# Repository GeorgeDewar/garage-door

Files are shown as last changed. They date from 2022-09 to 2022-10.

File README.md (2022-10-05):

# garage-door

ESP8266-based garage door controller (status and control via MQTT)

This is a personal project to control my garage door opener remotely using my phone. It's designed specifically around my garage door opener, which is pretty old and I'm not even sure what make and model it is. It comprises a circuit containing a NodeMCU ESP8266 dev board, some components, and a small modification to the door opener to expose additional signals.

My opener has a series of screw terminals, notably:

- GND - common ground for all other terminals
- P/B (push button) - a 5V signal that when pulled low, causes the door to open or close. I believe it is equivalent to the button on the side of the unit
- 15V - a supply of power, which is poorly regulated so is often more like 18-20V

I had two goals. Firstly, to install a button inside the house with an LED that shows the status of the door.  For that I used the [PDL 680TMNPB-WH](https://www.scottelectrical.co.nz/shop/switch-gear-wiring-devices/modulesmechs/specialty/pdl-switch-elv-tactile-red-neon/) which combines a momentary switch (button) with an LED. But the LED has a built-in resistor such that it is designed to take a 24V input, which means I can't drive it easily from a microcontroller. So, I elected to use the 15V supply to power the LED. In fact, even with 5V the LED is visible, but dim. 15-20V is good and bright.

The LED is on when the door is open, flashing when it is partially open (e.g. opening or closing), and off when it is closed. The button is connected directly (electrically speaking) to the P/B terminal on the garage door so that it will work even if my device is unpowered.

The second goal is to control it from my phone. That means being able to see the status, and actuate the door. To achieve this, I made the microcontroller send to Home Assistant via MQTT status updates, and accept commands, which cause it to pull the P/B signal low to simulate a button press.

The list of terminals I gave above did not include any terminal which can be used to detect the state of the door. But the opener does have two microswitches that are actuated by cams to tell it when it has fully closed or fully opened. These are also 5V signals that are pulled low by the microswitches. I tapped into these and exposed them, along with the other three termials, on a convenient DB9 socket which I mounted on the opener. Using these two signals, my microcontroller can tell if the door is open, closed, or partially open. The fourth state, where both signals are low, should never occur.

This repository contains the firmware for the ESP8266, and the circuit diagram and veroboard layout I used. I designed in support for end-user WiFi setup, but unfortunately the MQTT settings are hard-coded. I don't know if I will ever bother to change that since I am not highly likely to have additional users to support, and if I do get some, they can just change the code.

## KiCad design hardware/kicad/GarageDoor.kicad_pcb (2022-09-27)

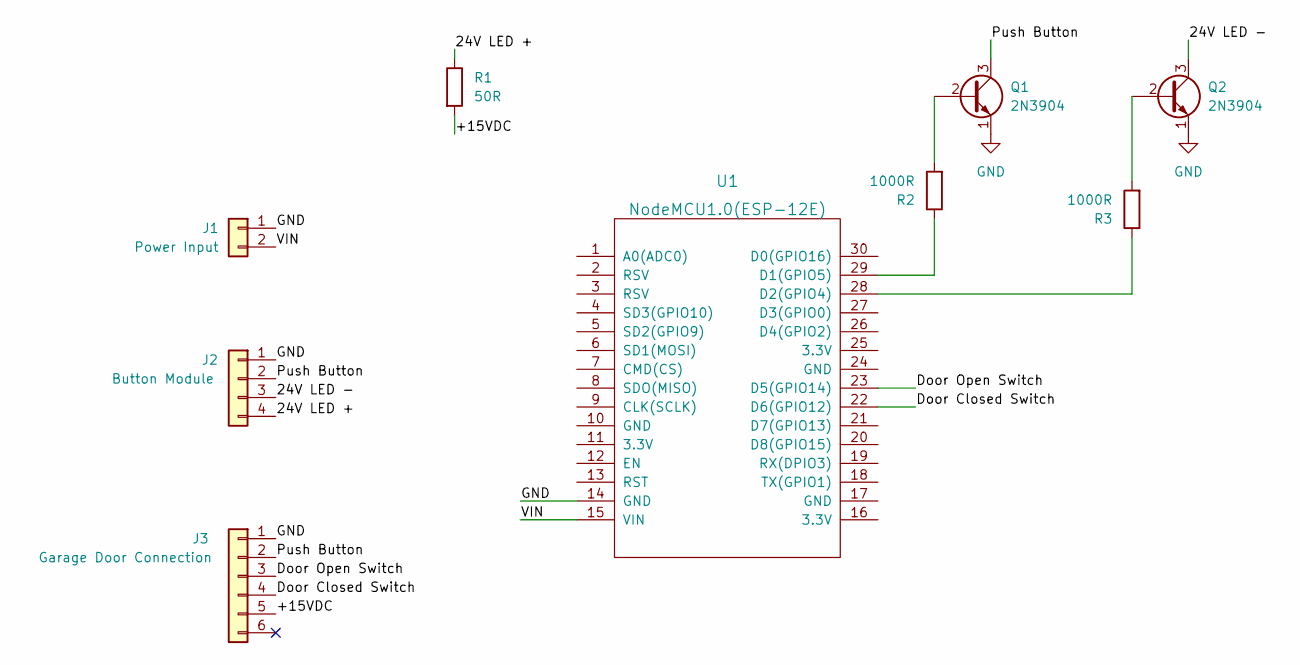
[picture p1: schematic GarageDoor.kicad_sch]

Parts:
J1: Power Input; PinHeader_1x02_P2.54mm_Vertical
J2: Button Module; PinHeader_1x04_P2.54mm_Vertical
J3: Garage Door Connection; PinHeader_1x06_P2.54mm_Vertical
Q1, Q2: 2N3904; TO-92_Inline
R1: 50R; R_Bare_Metal_Element_L16.3mm_W4.8mm_P15.30mm
R2, R3: 1000R; R_Bare_Metal_Element_L16.3mm_W4.8mm_P15.30mm
U1: NodeMCU1.0(ESP-12E); NodeMCU1.0(12-E)

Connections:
/24V LED +: J2.4, R1.1
/24V LED -: J2.3, Q2.3 (C)
/+15VDC: J3.5, R1.2
/Door Closed Switch: J3.4, U1.22 (D6(GPIO12))
/Door Open Switch: J3.3, U1.23 (D5(GPIO14))
/Push Button: J2.2, J3.2, Q1.3 (C)
/VIN: J1.2, U1.15 (VIN)
GND: J1.1, J2.1, J3.1, Q1.1 (E), Q2.1 (E), U1.14 (GND)
unnamed: Q1.2 (B), R2.2
unnamed: Q2.2 (B), R3.2
unnamed: R3.1, U1.28 (D2(GPIO4))
unnamed: R2.1, U1.29 (D1(GPIO5))

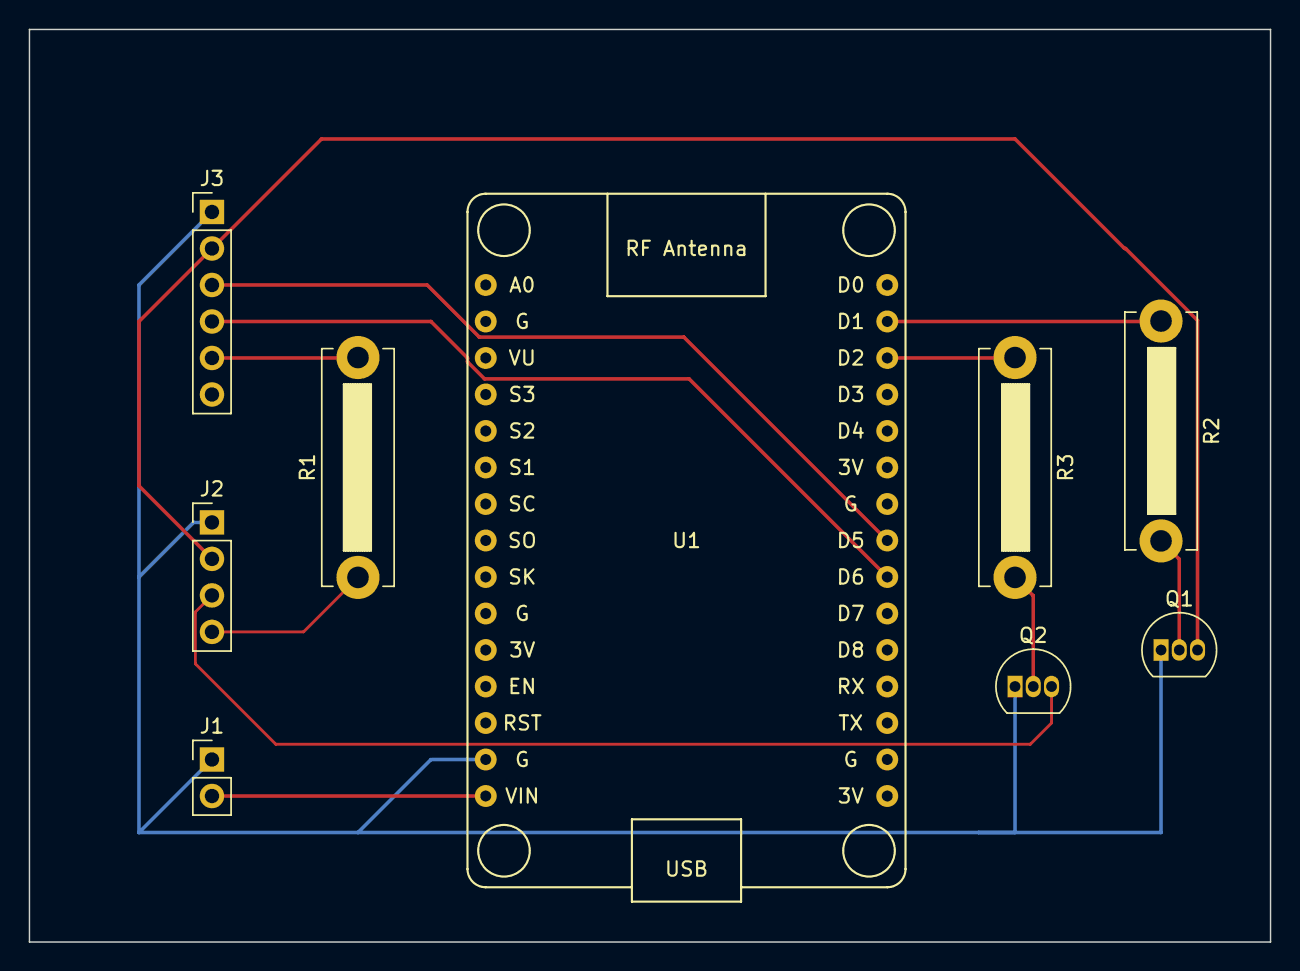
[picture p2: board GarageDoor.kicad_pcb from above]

Board: 2 copper layers, 86.4 x 63.5 mm, 9 parts (0 on the bottom side), 12 nets.

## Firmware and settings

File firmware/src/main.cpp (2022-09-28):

#include <ESP8266WiFi.h>
#include <WiFiManager.h>
#include <EasyButton.h>
#include <EspMQTTClient.h>

// NodeMCU board pins
#define BUTTON_FLASH        D3
#define OUTPUT_PUSH_BUTTON  D1
#define OUTPUT_24V_LED      D2
#define INPUT_DOOR_OPEN     D5
#define INPUT_DOOR_CLOSED   D6

// Flashing speeds
#define FLASHING_SLOW_MS    500
#define FLASHING_FAST_MS    250

// Possible states for the door to be in, based on the microswitch positions
enum DoorState {
  OPEN,
  DOOR_CLOSED,
  PARTIAL,      // neither open nor closed, which means opening, closing, or just stopped part way
  INVALID,      // i.e. both open and closed, shouldn't be possible
  UNKNOWN       // the default state prior to reading it for the first time, or to force an update
};

// Objects
WiFiManager wifiManager;
EasyButton flashButton(BUTTON_FLASH);
EspMQTTClient mqttClient(
  "192.168.20.68",
  1883,            // It is mandatory here to allow these constructors to be distinct from those with the Wifi handling parameters
  "DVES_USER",     // Omit this parameter to disable MQTT authentification
  "DVES_PASS",     // Omit this parameter to disable MQTT authentification
  "GarageDoor");

// Variables
DoorState door_state = UNKNOWN;
unsigned long lastBlinkMillis = 0; // when the loop function last ran
int lastFlashingState = LOW;

// Interrupt service routine for the interrupt triggered by the Flash button
void flashButtonISR()
{
  flashButton.read();
}

// Callback function to be called when the Flash button is pressed. Erase all configuration.
void onFlashButtonPressed() {
  Serial.println("Flash button has been pressed! Resetting...");
  ESP.eraseConfig();
  delay(500);
  ESP.restart();
}

// Simulate a press of the open/close button
void pressDoorButton() {
  digitalWrite(OUTPUT_PUSH_BUTTON, HIGH); // depress the button
  delay(250);
  digitalWrite(OUTPUT_PUSH_BUTTON, LOW); // back to high impedance
}

// Called when MQTT connection established
void onConnectionEstablished()
{
  // Subscribe to commands. For any command, we press the button. That's all we can do.
  mqttClient.subscribe("garage-door/command", [](const String & payload) {
    Serial.println(payload);
    pressDoorButton();
  });

  // Announce that we are online
  mqttClient.publish("garage-door/availability", "online");

  // Force a status update, in case we've been offline for a while
  door_state = DoorState::UNKNOWN;
}

// Flash the internal LED the specified number of times
void flashBuiltInLed(int times) {
  for(int i=0; i<times; i++) {
    digitalWrite(LED_BUILTIN, LOW);
    delay(200);
    digitalWrite(LED_BUILTIN, HIGH);
    if (i < times) delay(200);
  }
}

// Called once on startup
void setup() {
  // Initialise our inputs and outputs
  pinMode(BUTTON_FLASH, INPUT_PULLUP);
  pinMode(LED_BUILTIN, OUTPUT);
  pinMode(OUTPUT_PUSH_BUTTON, OUTPUT);    // note: when low, the external transistor is high impedance (floating)
  pinMode(OUTPUT_24V_LED, OUTPUT);        // note: when low, the external transistor is high impedance (floating)
  pinMode(INPUT_DOOR_OPEN, INPUT);
  pinMode(INPUT_DOOR_CLOSED, INPUT);

  // Write the initial states of our outputs
  digitalWrite(LED_BUILTIN, LOW);         // Turn the LED on
  digitalWrite(OUTPUT_PUSH_BUTTON, LOW);  // Don't be pressing the button
  digitalWrite(OUTPUT_24V_LED, LOW);      // Main LED off to start with

  // Begin serial communication for debugging
  Serial.begin(115200);

  // Work out and announce our device name
  String deviceName = "GarageDoor-" + String(ESP.getChipId(), HEX);
  Serial.print("\nHello! Device name = ");
  Serial.println(deviceName);

  // Captive portal for first-time WiFi setup
  wifiManager.setConfigPortalTimeout(120); // after two minutes, give up on connecting
  if (wifiManager.autoConnect(deviceName.c_str(), NULL)) {
    // We're connected, so we set the host name and announce our IP address
    WiFi.hostname(deviceName);
    Serial.println("WiFi connected: IP = " + WiFi.localIP().toString());

    // Always run the web portal so the device can be reconfigured
    wifiManager.startWebPortal();
  } else {
    Serial.println("Failed to connect to WiFi; in offline mode");
  }

  // Configure the MQTT client
  mqttClient.enableDebuggingMessages();
  mqttClient.enableLastWillMessage("garage-door/availability", "offline");

  // Configure the Flash button
  flashButton.begin();
  flashButton.onPressed(onFlashButtonPressed);
  flashButton.enableInterrupt(flashButtonISR);

  // Flash built-in LED to indicate startup complete
  flashBuiltInLed(3); // really 2 flashes as LED already on
}

// the loop function runs over and over again forever
void loop() {
  // Let the libraries do their processing
  flashButton.read();
  wifiManager.process();
  mqttClient.loop();

  // Determine the state of the door based on the microswitches
  int doorClosed = digitalRead(INPUT_DOOR_CLOSED);
  int doorOpen = digitalRead(INPUT_DOOR_OPEN);
  DoorState new_state;
  if (doorClosed == LOW && doorOpen == HIGH) {
    new_state = DoorState::DOOR_CLOSED;
  } else if (doorClosed == HIGH && doorOpen == LOW) {
    new_state = DoorState::OPEN;
  } else if (doorClosed == HIGH && doorOpen == HIGH) {
    new_state = DoorState::PARTIAL;
  } else {
    new_state = DoorState::INVALID;
  }

  // Handle the LED output
  if (new_state == DoorState::DOOR_CLOSED) {
    digitalWrite(OUTPUT_24V_LED, LOW);
  } else if (new_state == DoorState::OPEN) {
    digitalWrite(OUTPUT_24V_LED, HIGH);
  } else {
    // we are flashing
    unsigned long currentTime = millis();
    if (currentTime > lastBlinkMillis + FLASHING_SLOW_MS) {
      lastBlinkMillis = currentTime;
      lastFlashingState = 1 - lastFlashingState;
      digitalWrite(OUTPUT_24V_LED, lastFlashingState);
    }
  }

  // If nothing has changed, then there's nothing else we need to do
  if (door_state == new_state) return;

  // Figure out what message to publish based on the old and new state
  // Publishing will do nothing if the client is not connected
  if (new_state == DoorState::DOOR_CLOSED) {
    Serial.println("Door has closed");
    mqttClient.publish("garage-door/state", "closed");
  } else if (new_state == DoorState::OPEN) {
    Serial.println("Door has opened");
    mqttClient.publish("garage-door/state", "open");
  } else if (new_state == DoorState::PARTIAL && door_state == DoorState::OPEN) {
    // transition from OPEN to PARTIAL means we are closing
    Serial.println("Door is closing");
    mqttClient.publish("garage-door/state", "closing");
  } else if (new_state == DoorState::PARTIAL && door_state == DoorState::DOOR_CLOSED) {
    // transition from CLOSED to PARTIAL means we are opening
    Serial.println("Door is opening");
    mqttClient.publish("garage-door/state", "opening");
  } else if (new_state == DoorState::PARTIAL && door_state == DoorState::UNKNOWN) {
    // it must have been partially open on start-up
    Serial.println("Door is partially open, assuming closing");
    mqttClient.publish("garage-door/state", "closing");
  } else if (new_state == DoorState::INVALID) {
    // we have a problem
    Serial.println("Door state is invalid (both microswitches LOW)");
    mqttClient.publish("garage-door/state", "closing");
  }

  // Now update door_state since we don't need the old value any more
  door_state = new_state;
}

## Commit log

2022-09-26 Get LED output working right
2022-09-26 Remove old Arduino IDE based version
2022-09-27 Add Kicad files
    [GarageDoor.kicad_pcb, GarageDoor.kicad_sch]
